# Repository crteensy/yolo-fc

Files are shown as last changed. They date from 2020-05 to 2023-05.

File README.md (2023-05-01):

# Yolo FC, STM32F7, 2-6S
This FC has been test flown with a 3" quad, and it flew well. flight logs of the maiden flight are in /logs

- Main MCU: STM32F745
- IMU: ICM-20602
- Flash: 8MB
- Baro: BMP280
- OSD: '7456
- GNSS: Integrated GPS module (uBlox ZOE-M8Q) with u.Fl connector and experimental support for active antennas
- 4 ESCs:
  - EFM8BB21 / bluejay
  - Calculated current rating of 20A continuous 30A burst (depending on the airflow cooling situation)
- Current sensor: INA186 with 0m5 shunt - subjectively some of the best current measurements we have seen on any FC
- 4 multi purpose expansion connectors:
  - each with its own UART
  - shared I2C bus
  - 5V, 3V3 and GND
  - a multi-purpose pin for analog RSSI, Buzzer, LEDs, etc.
- One video expansion connector:
  - Camera in and VTx out
  - UART
  - 2 multi-purpose pins
  - switchable 5V (*)
- size: 30 x 25.2 mm

The expansion connectors can be used with very simple or more complex plug-ins for
- Rx of your choice
- Magnetometer
- Buzzer
- LED strip
- dual camera switching on the OSD connector
- even additional plugin ESCs for hexa- and octocopters are possible

*) The OSD connector has a 5V output that is only ON when USB is not plugged in. This protects your USB port from power hungry VTx'es that might overload the port. However, that feature can be disabled with a solder bridge.

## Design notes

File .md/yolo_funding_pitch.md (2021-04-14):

# Please Help us Make the Final Yolo FC Prototype Fly

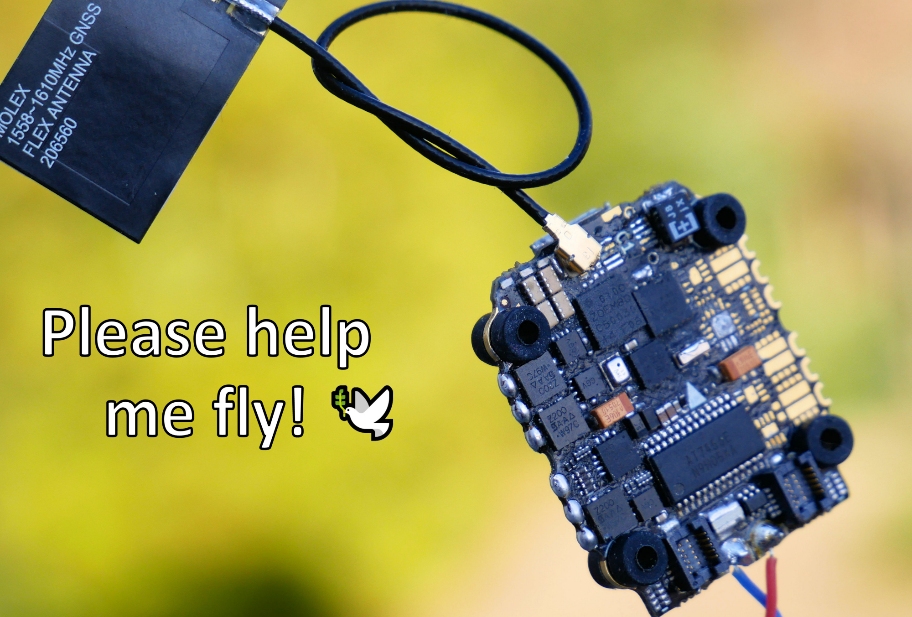
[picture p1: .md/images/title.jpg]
Manually assembled first prototype with GNSS Antenna

First partly by hand assembled prototype of the Yolo. More images at the end of the site.

## The YOLO AIO Flight Controller
The Yolo FC is an 20mm 25A F7 all-in-one flight controller. Initially, it was taylored to fullfill the needs of flight time record-breaking quads, but due to our urge to integrate more and more features made became the most versatile flight controller we can imagine. 
We somehow managed to assemble all functional parts of the first prototype by hand(!) in order to verify their function. For the next step, a second Prototype, we've come to an end of our manual assembly capabilities as well as our financial budget for PCBs and electronic parts. We see electronics design as part of our RC hobby and we don't intend to make any money with this, but our financial capacity is therefore also limited.
Please support us wit a small donation to make the Yolo finally fly!
[GOFUNDME LINK]

## The Specs 
It's actually two AIO FCs for two different battery voltage ranges:
- 1-3S
- 2-6S

What they have in common:
- Main MCU: STM32F745
- IMU: ICM-20602
- Flash: 8MB
- Baro: BMP280
- OSD: '7456 
- GNSS: Integrated GPS-module (uBlox ZOE-M8Q) with u.Fl connector and experimental support for active antennas
- 4 ESCs:
  - BLHeli_S bluejay with a custom firmware
  - Calculated current rating of 20A continuous 30A burst (depending on the airflow cooling situation)
  - up to now, we could only test one ESC with 16 A continuous (> 1 minute), but the whole FC got only slightly warm at this test
- Current sensor: INA186 with 0m5 shunt - subjectively some of the best current measurements we have seen on any FC
- 4 multi purpose expansion connectors:
  - each with its own UART
  - shared I2C bus
  - 5V, 3V3 and GND
  - a multi-purpose pin for analog RSSI, Buzzer, LEDs, etc.
- One video expansion connector:
  - Camera in and VTx out
  - UART
  - 2 multi-purpose pins
  - switchable 5V (*)
- size: 30 x 25.2 mm
- weight: about 4.4 grams + expansions

The expansion connectors can be used with very simple or more complex plug-ins for
- Rx of your choice
- Magnetometer
- Buzzer
- LED strip
- dual camera switching on the OSD connector
- even additional ESC adapters for hexa- and octocopters are possible

*) The OSD connector has a 5V output that is only ON when USB is not plugged in. This protects your USB port from power hungry VTx'es that might overload the port. However, that feature can be disabled with a solder bridge.

The first prototype was assembled manually, on a PCB that we were able to get for free because we had a huge amount of luck. However, it was not perfect, so:
- we want to make a revised layout and have it made
- but we don't want to assemble it manually again for sanity reasons.

Bcause we always have some additional cool RC projects in the pipeline, the prototyping PCB run might also contain:
- enough Yolo PCBs for a prototype batch (if it flies)
- complex YOLO expansions like a 2in1 and a 4in1 ESC for hexas and octos (Why no 45g AUW Hexa Whoop with GPS? Yes the more stupid it sounds, the more fun we have!:-) )
- crteensy's experiments with Cypress PSoC6 for an AIO controller that unifies FC, 4 ESCs and the OSD on one chip (yes, memory mapped ESCs!) in two sizes:
  - whoop for manual assembly, with Bluetooth and USB
  - 16 mm, Bluetooth only
- maybe an H7-Yolo with AM32 ESCs
- maybe an H7 1s tiny whoop board
- (some Express LRS prototypes)

We think that for high quality PCB Panels with custom Layer Stackup and Via in Pad we need about 1500$. A professional prototype assembly of a few flight controllers and the compontens will be about 2500$. If we get more donations than we actually need and The Yolo flies, we will assemble more and send them to testers and  randomly picked donors (we need an e-mail adress in this case).

We don't have any support from the industry, we don't intend to make money with this and all designs will be open hardware for everyone to manufacture.

# Pictures
Current Yolo prototype:

Expansions:

PSoC Whoop board rendering (top/bottom):

PsoC 16 mm board rendering (top/bottom):

ELRS:

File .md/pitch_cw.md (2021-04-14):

## Please help us make the final Yolo FC prototype fly

What started out as a hobby project has brought us to end of our manual assembly capabilities, but we've gotten pretty far with our AIO:

[yolo-pic]

(more pictures at the end of this post)

# The Yolo FC
It's actually two AIO FCs for two different battery voltage ranges:
- 1-3S
- 2-6S

What they have in common:
- Main MCU: STM32F745
- IMU: ICM-20602
- Flash: 8MB
- Baro: BMP280
- OSD: '7456 
- GNSS: uBlox ZOE-M8Q with u.Fl connector and experimental support for active antennas
- 4 ESCs:
  - BLHeli_S bluejay with a custom layout
  - we could only test it to 16 A continuous (> 1 minute) until now, and it didn't burn
- Current sensor: INA186 with 0m5 shunt
- 4 multi purpose expansion connectors:
  - each with its own UART
  - shared I2C bus
  - 5V, 3V3 and GND
  - a multi-purpose pin
- One video expansion connector:
  - Camera in and VTx out
  - UART
  - 2 multi-purpose pins
  - switchable 5V (*)
- size: 30 x 25.2 mm
- weight: about 4.2 grams + expansions

The expansion connectors can be used with very simple or more complex plug-ins for
- Rx of your choice
- Magnetometer
- Buzzer
- LED strip
- in the next layout revision: additional
  - 2in1 ESC for hex copters
  - 4in1 ESC for octo copters
- dual camera switching on the OSD connector

*) The OSD connector has a 5V output that is only ON when USB is not plugged in. This protects your USB port from power hungry VTx'es that might overload the port. However, that feature can be disabled with a solder bridge.

The first prototype was assembled manually, on a PCB that we were able to get for free because we had a huge amount of luck. However, it was not perfect, so:
- we want to make a revised layout and have it made
- but we don't want to assemble it manually again for sanity reasons.

The prototyping run will also contain boards for:
- complex expansions like a 2in1 and a 4in1 ESC
- crteensy's experiments with Cypress PSoC6 for an AIO controller that unifies FC, 4 ESCs and the OSD on one chip (yes, memory mapped ESCs!) in two sizes:
  - whoop for manual assembly, with Bluetooth and USB
  - 16 mm, Bluetooth only
- (some Express LRS prototypes)
- enough Yolo PCBs for a first production run (if it flies)

However, that prototyping panel will be expensive, so we are asking for financial support on [GOFUNDME LINK] to get the PCBs made and a handful of Yolos assembled profesionally; also to send them to testers and random supporters (if we have enough).
If you want to support us, please donate.

We don't have any support from the industry, we don't intend to make money with this and all designs will be open hardware.

# Pictures
Current Yolo prototype:

Expansions:

PSoC Whoop board rendering (top/bottom):

PsoC 16 mm board rendering (top/bottom):

ELRS:

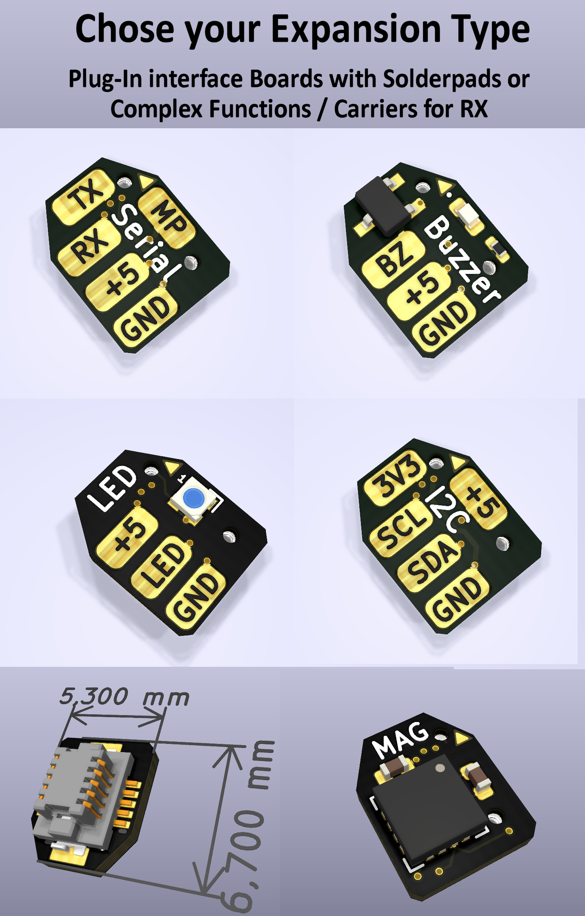
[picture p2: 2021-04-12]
.md/images/expansion_connectors.png

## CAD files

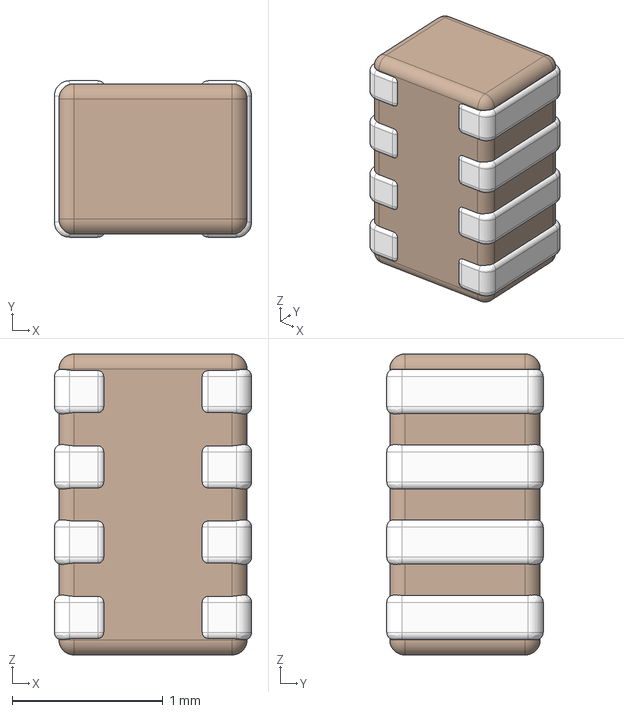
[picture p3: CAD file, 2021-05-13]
kicad/3D/idc.stp
1.31 x 1.04 x 2.00 mm

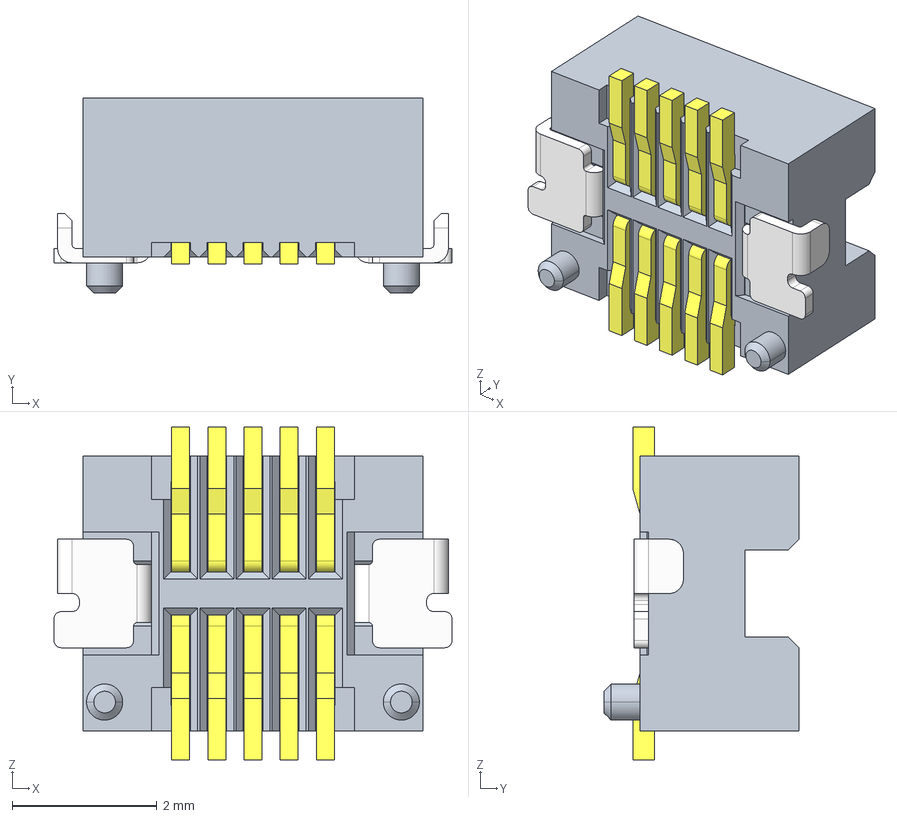
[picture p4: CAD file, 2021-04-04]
kicad/3D/10132797-011100LF.stp
5.50 x 2.70 x 4.60 mm
30H-10PIN-F-H
30H-F-TERMINAL x 5

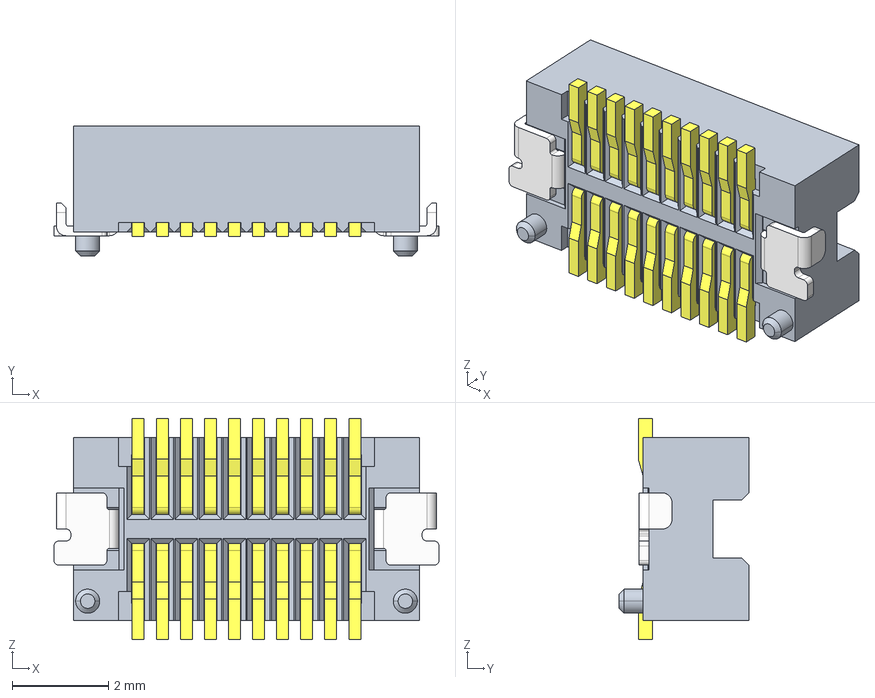
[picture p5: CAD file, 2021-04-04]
kicad/3D/10132797-021100LF.stp
8.00 x 2.70 x 4.60 mm
30H-20PIN-F-H
30H-F-TERMINAL x 10

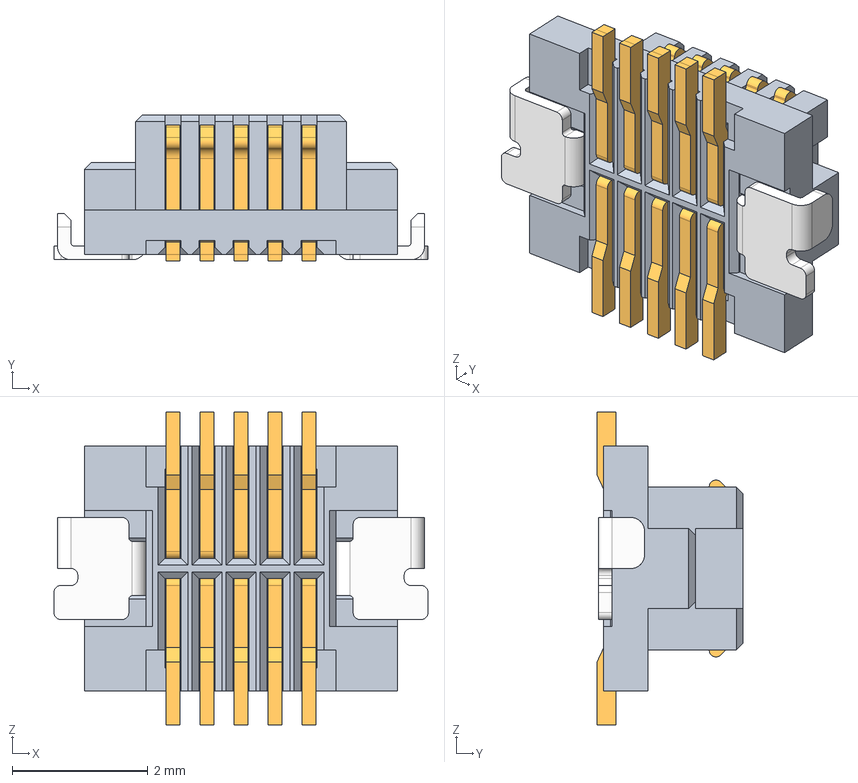
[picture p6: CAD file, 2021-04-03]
kicad/3D/10132798-011110LF.stp
5.50 x 2.15 x 4.60 mm
30H-10PIN-M-H
30H-M-TERMINAL x 5

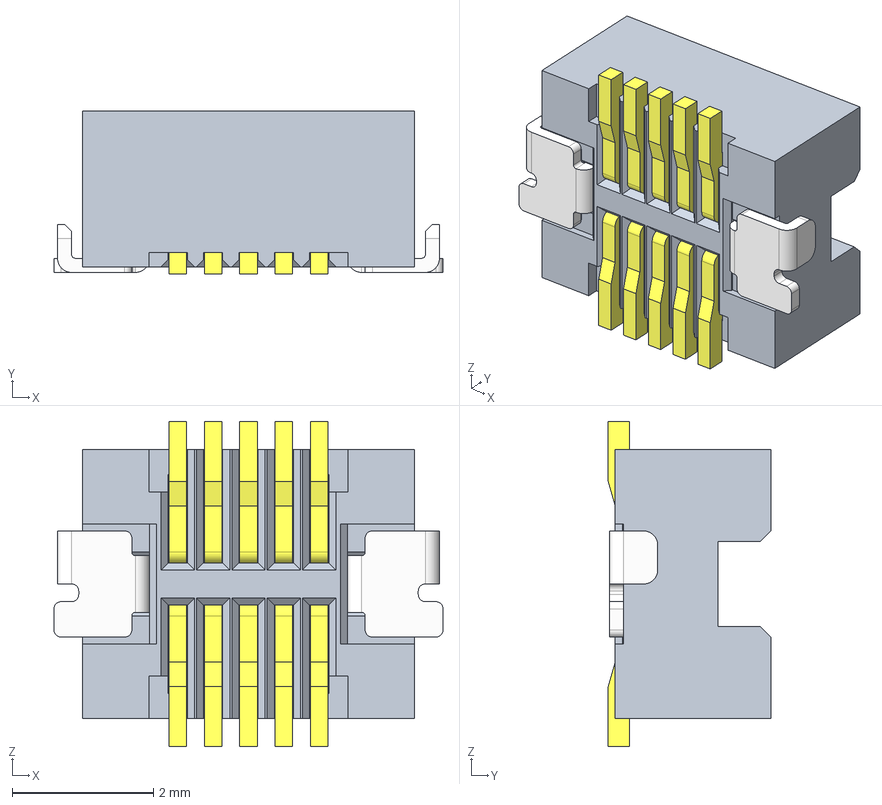
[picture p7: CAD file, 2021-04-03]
kicad/3D/10132797-011110LF.stp
5.50 x 2.30 x 4.60 mm
30H-10PIN-F-H
30H-F-TERMINAL x 5

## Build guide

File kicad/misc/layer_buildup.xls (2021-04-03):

Layer | Type | Thickness
Top | Cu 35µm | 35
 | 2x Prepreg 1080 or similar | 140
In1 | Cu 18µm | 18
 | Core 50 μm | 50
In2 | Cu 18µm | 18
 | 2x Prepreg 1080 or similar | 140
In3 | Cu 35µm | 35
 | Core 50 μm | 50
In4 | Cu 35µm | 35
 | 2x Prepreg 1080 or similar | 140
In5 | Cu 18µm | 18
 | Core 50 μm | 50
IN6 | Cu 18µm | 18
 | 2x Prepreg 1080 or similar | 140
Bot | Cu 35µm | 35
 |  | 922

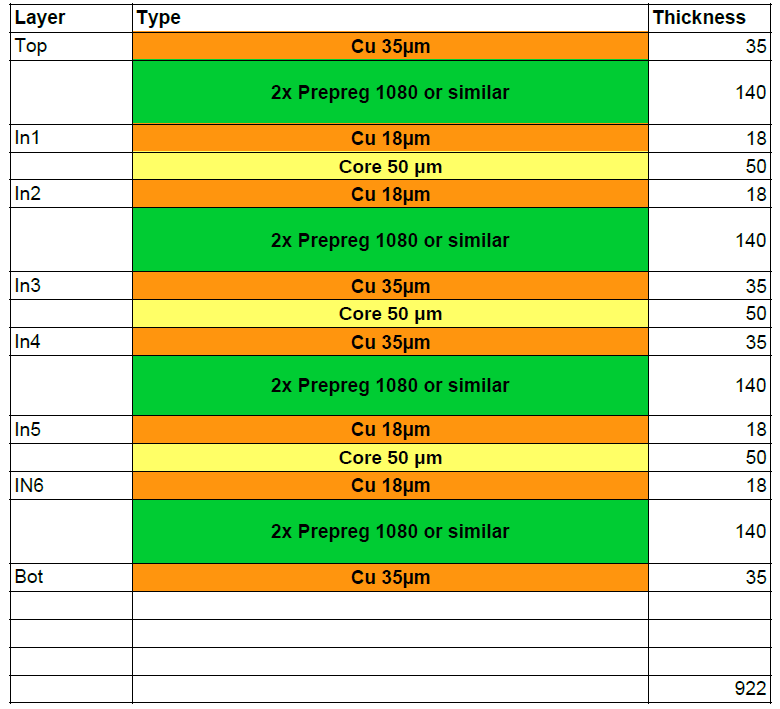
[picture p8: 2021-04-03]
kicad/misc/layer_buildup.png

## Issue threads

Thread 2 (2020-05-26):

Add VUSB voltage divider

crteensy, 2020-05-26:
correct operation needs a V divider from VUSB to sense input

Closed 2023-05-01.

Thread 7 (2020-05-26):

Slightly optional: buzzer output

crteensy, 2020-05-26:
Add buzzer driver FET or provide other means of connecting a buzzer

Closed 2023-05-01.

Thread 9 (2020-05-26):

Clarify ADC full scale input voltage

crteensy, 2020-05-26:
Schematic is drawn for 1.2V full scale, check in BF sources if that's correct.

Closed 2023-05-01.

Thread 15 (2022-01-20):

Fix RN 4x0402 array footprint

crteensy, 2022-01-20:
Fix RN 4x0402 array footprint

Closed 2023-05-01.

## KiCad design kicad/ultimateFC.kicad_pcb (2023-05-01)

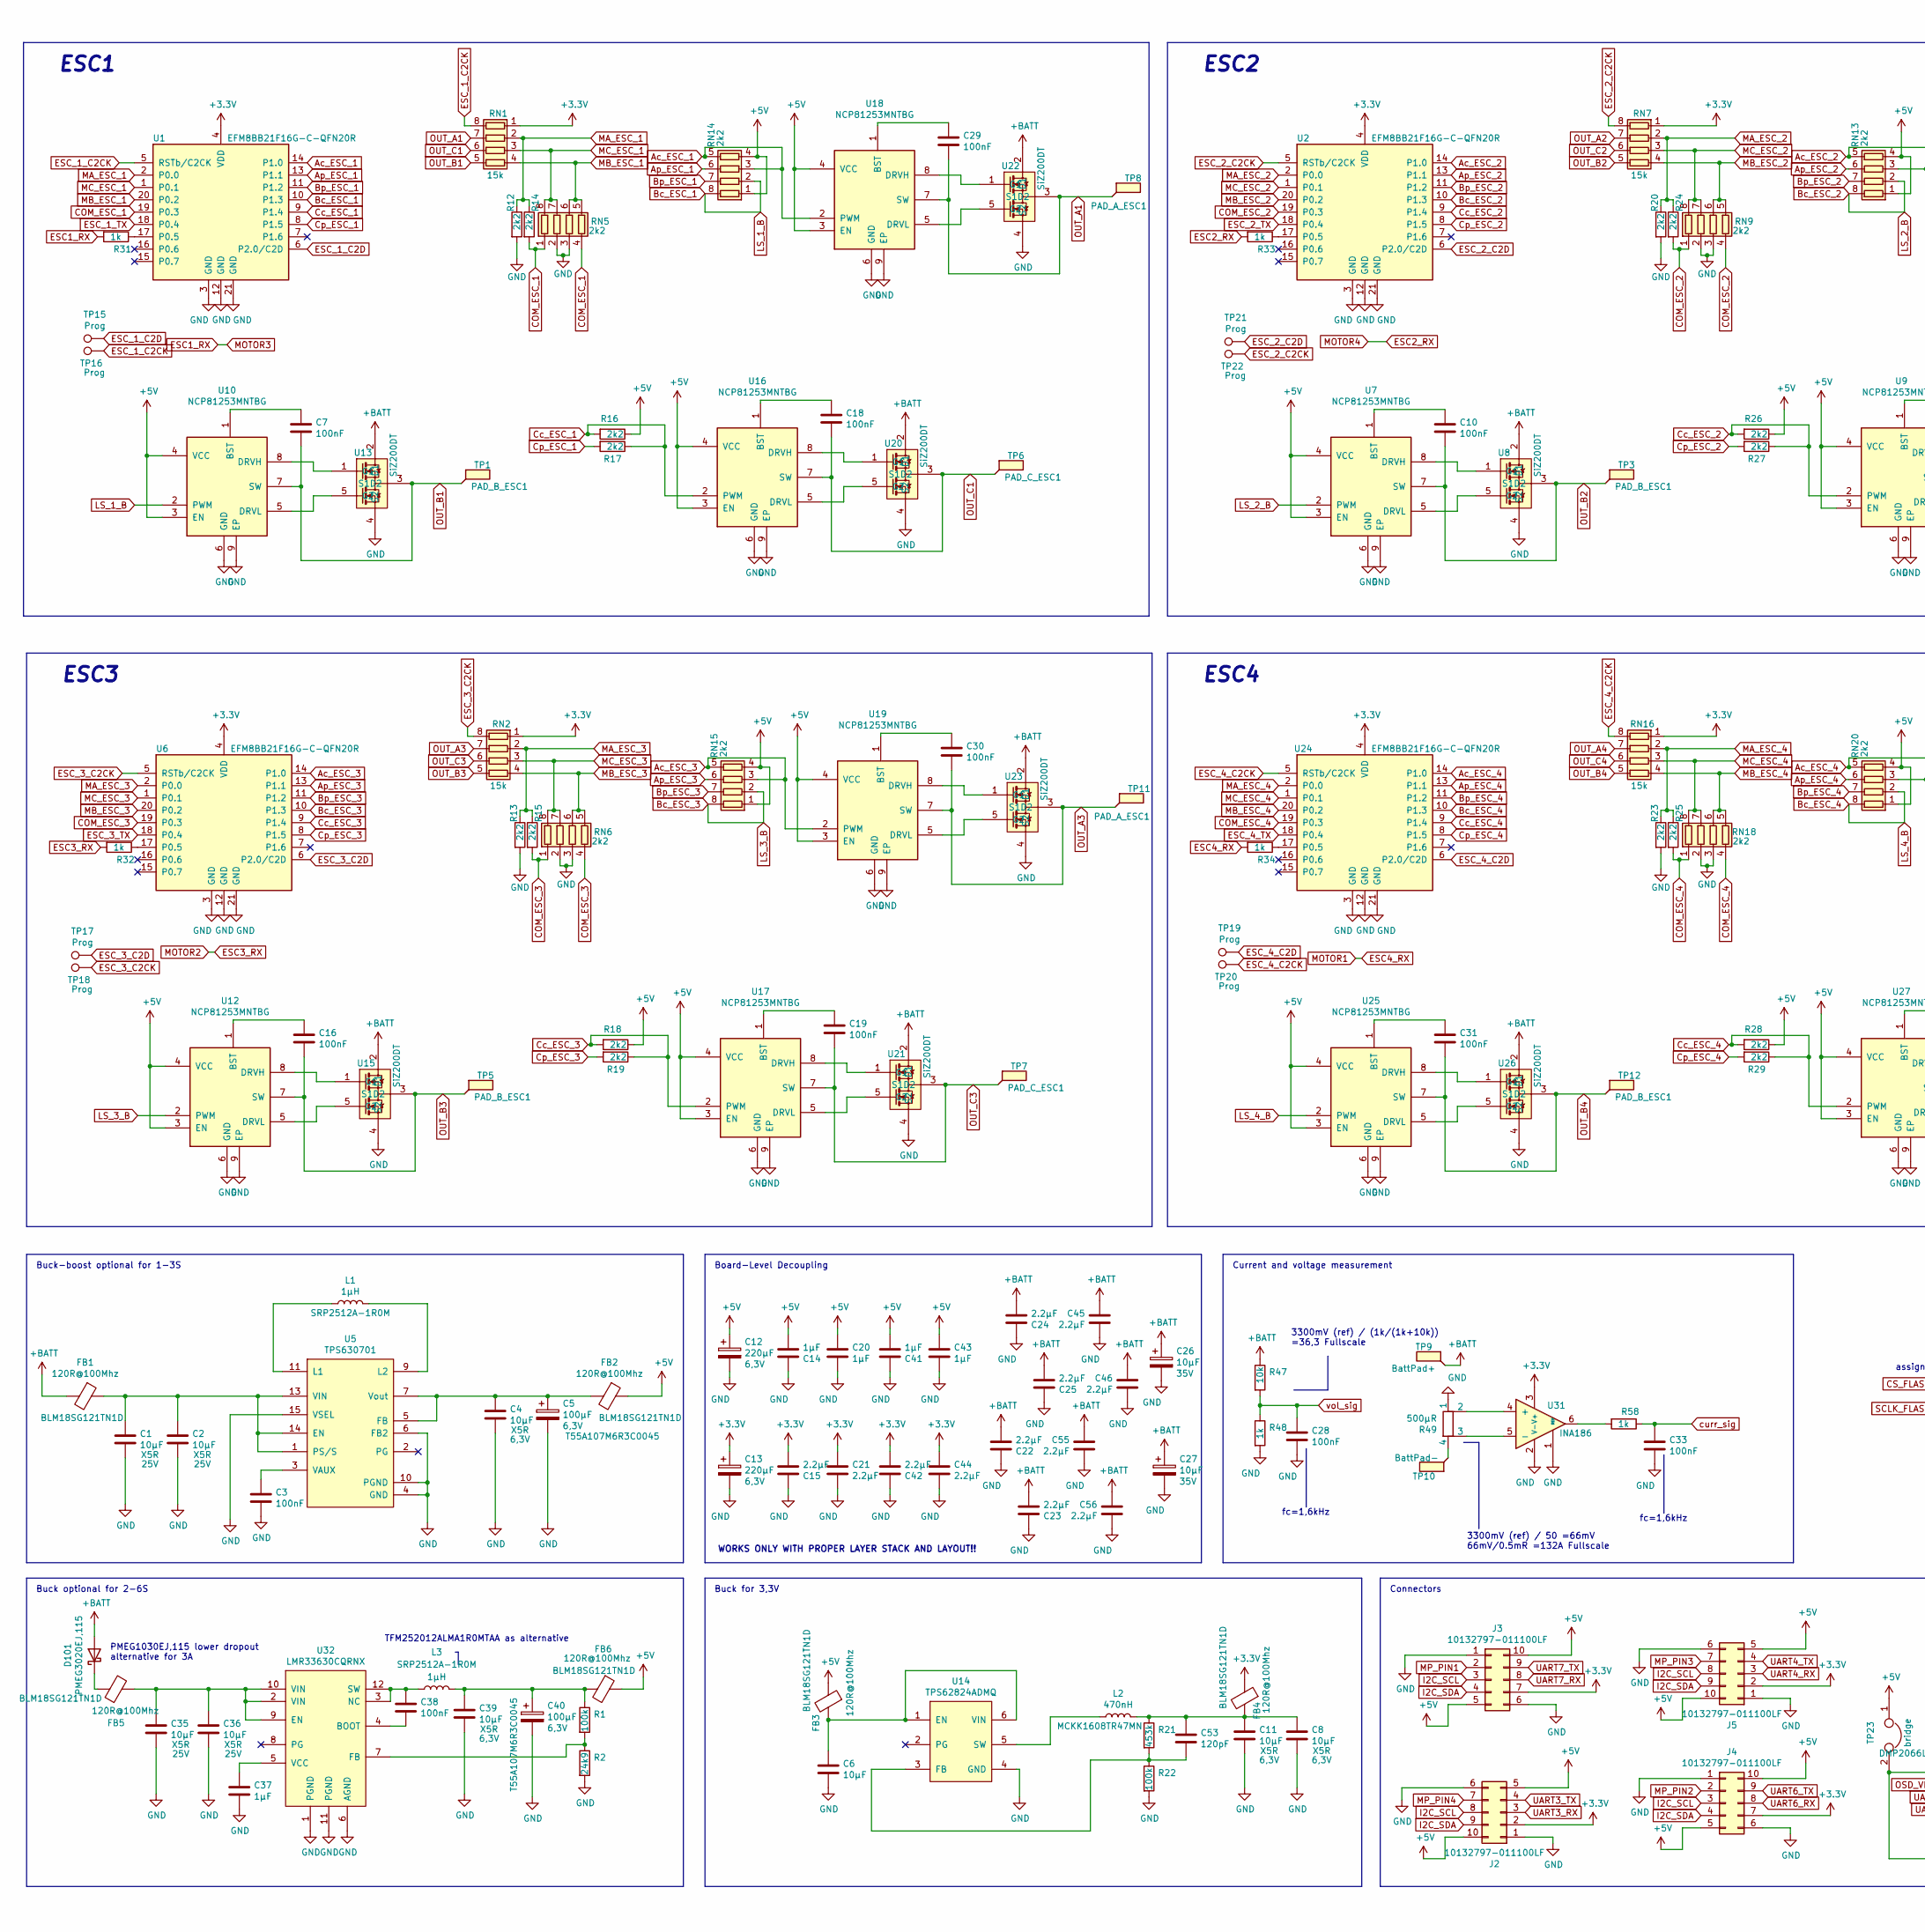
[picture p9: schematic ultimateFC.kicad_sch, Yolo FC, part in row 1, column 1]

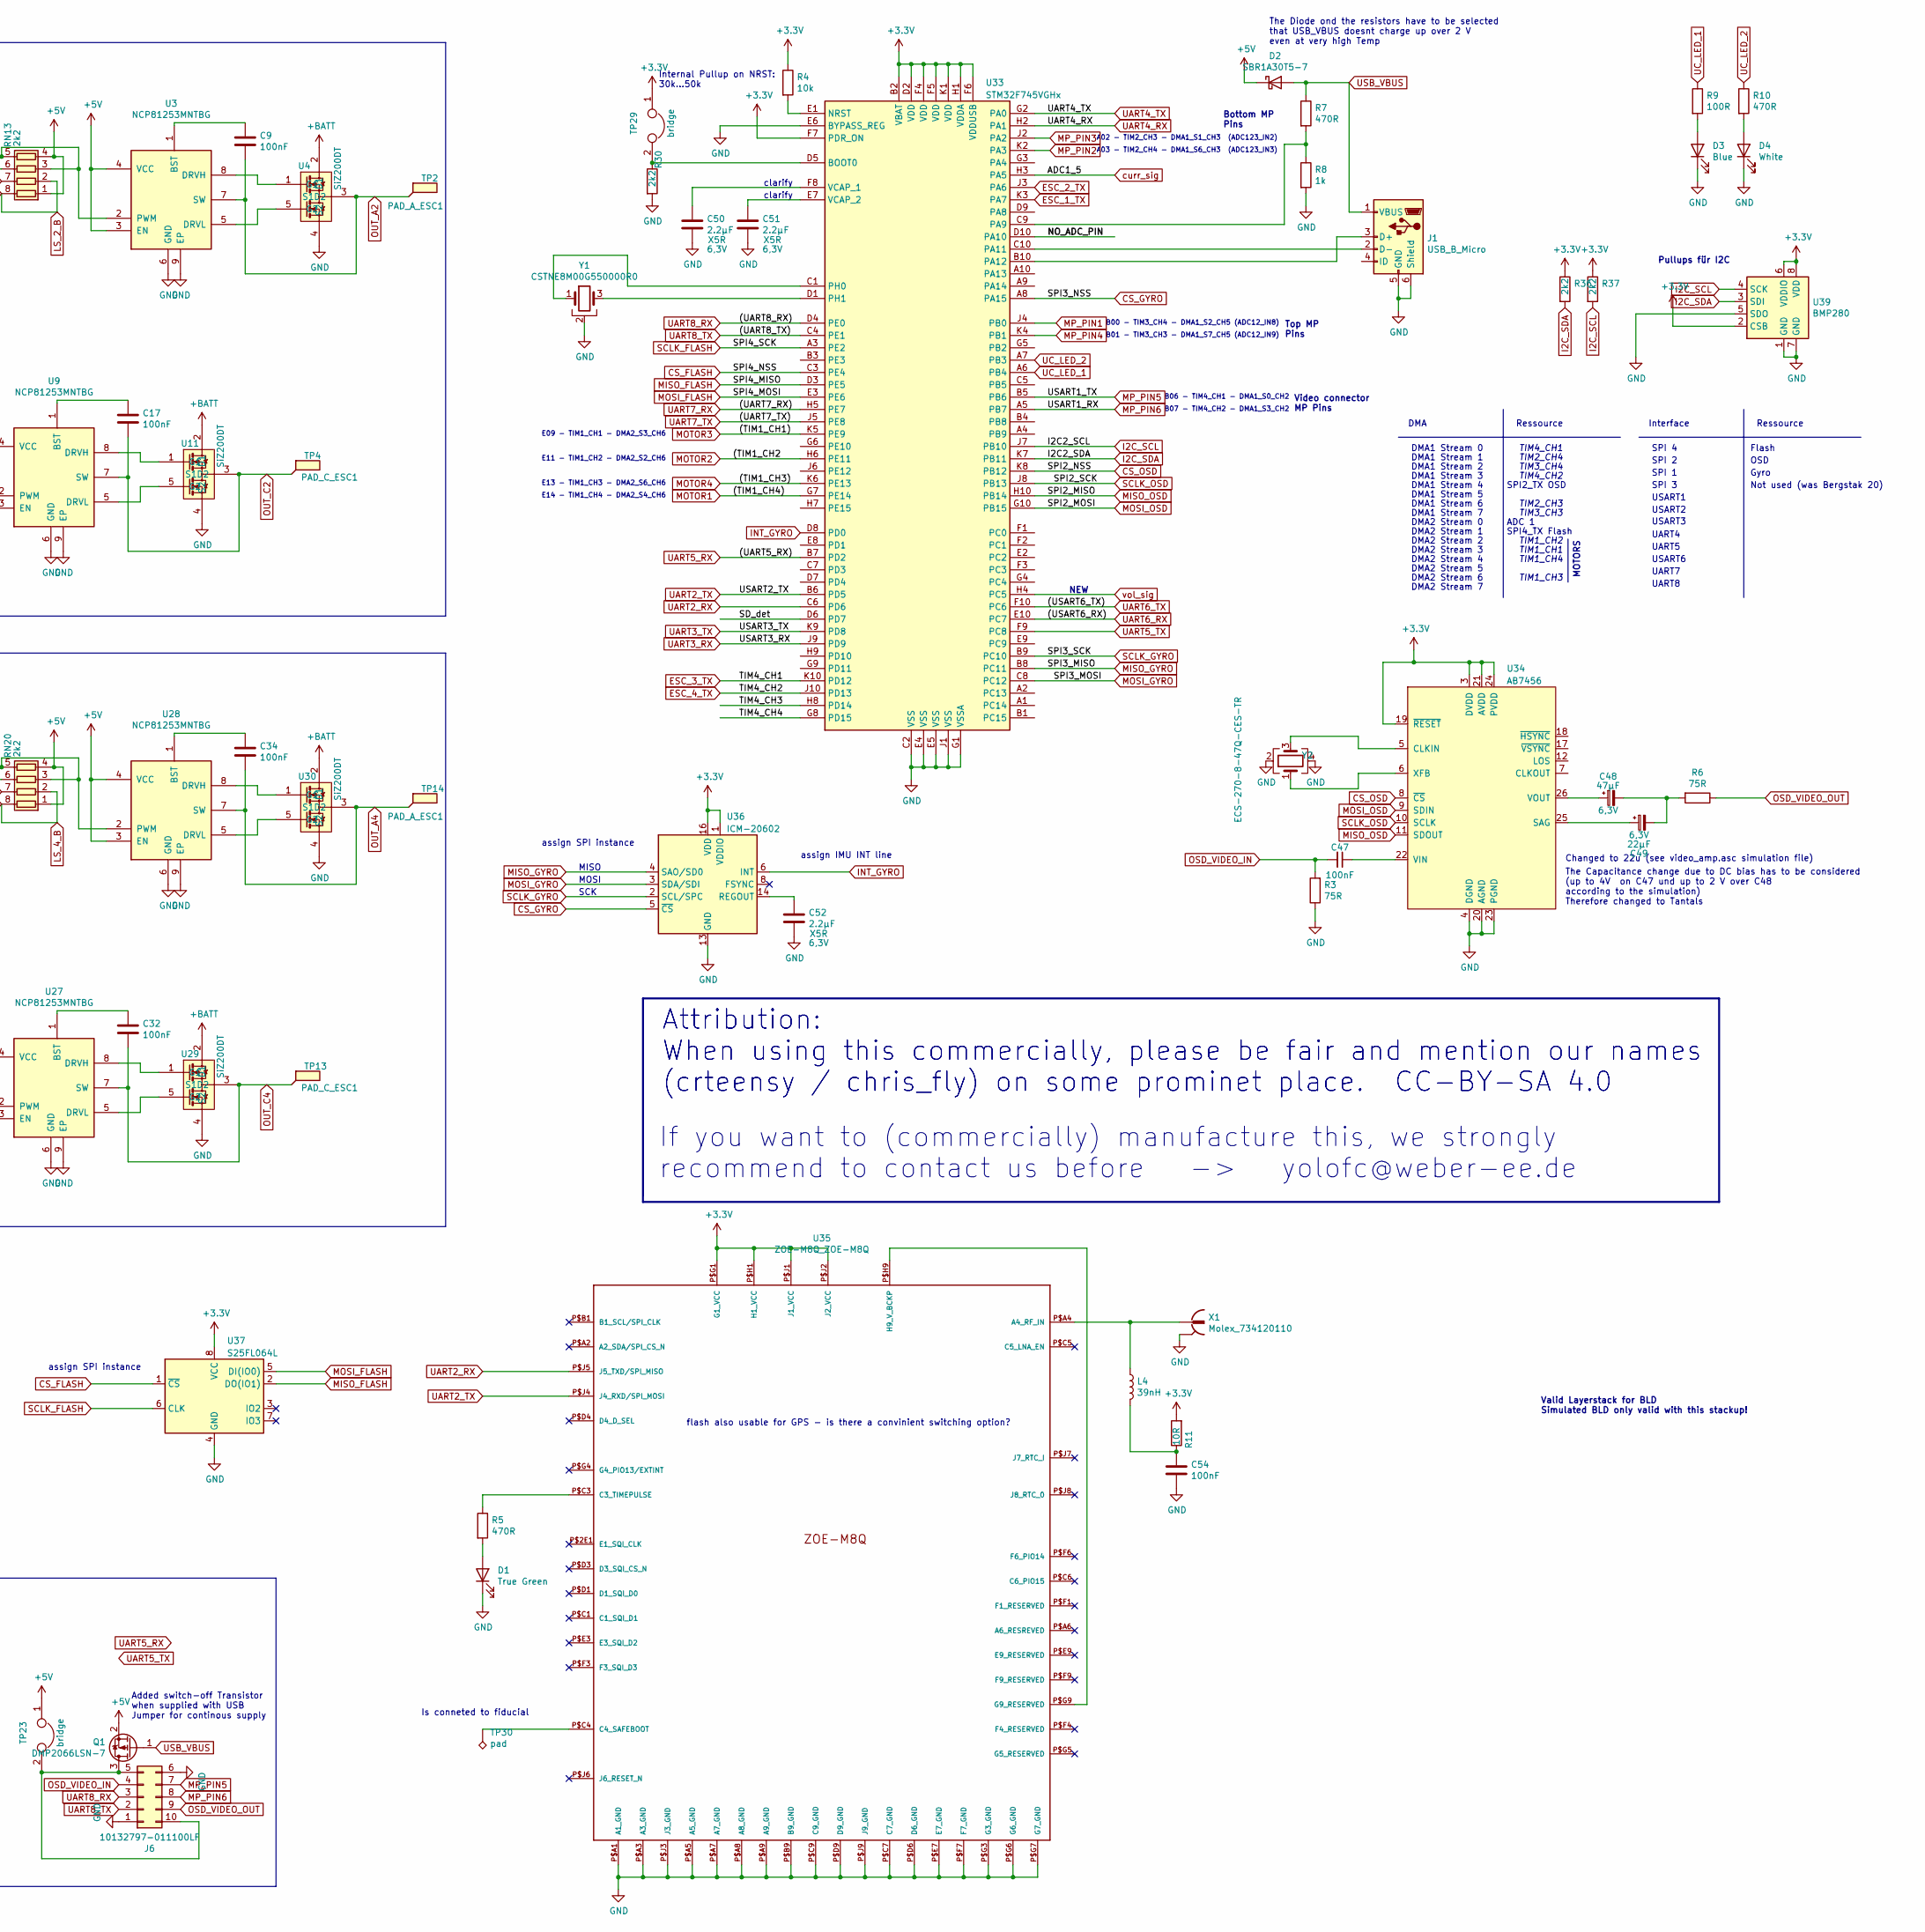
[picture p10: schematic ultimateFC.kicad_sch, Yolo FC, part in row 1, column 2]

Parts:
C1, C2, C35, C36: 10µF; C_1206_3216Metric
C3, C28, C33, C38, C47, C54: 100nF; C_0201_0603Metric_mod
C4, C6, C8, C11, C39: 10µF; C_0603_1608Metric
C5, C40: 100µF; CP_EIA-3216-10_Kemet-I
C7, C9, C10, C16, C17, C18, C19, C29, C30, C31, C32, C34: 100nF; C_0402_1005Metric
C12, C13: 220µF; CP_EIA-3528-15_AVX-H
C14, C20, C41, C43: 1µF; C_AVX_Super_Low_ESL
C15, C21, C42, C44: 2.2µF; C_AVX_Super_Low_ESL
C22, C23, C24, C25, C45, C46, C55, C56: 2.2µF; C_0603_1608Metric
C26, C27: 10µF; CP_EIA-3216-18_Kemet-A
C37: 1µF; C_0402_1005Metric
C48: 47µF; C_0603_1608Metric
C49: 22µF; C_0603_1608Metric
C50, C51, C52: 2.2µF; C_0402_1005Metric
C53: 120pF; C_0201_0603Metric_mod
D1: True Green; LED_0201_0603Metric
D2: SBR1A30T5-7; D_SOD-523
D3: Blue; LED_0201_0603Metric
D4: White; LED_0201_0603Metric
D101: PMEG3020EJ,115; D_SOD-323
FB1, FB2, FB3, FB4, FB5, FB6: 120R@100Mhz; L_0603_1608Metric
J1: USB_B_Micro; USB_Micro-B_Molex_47346-0001
J2, J3, J4, J5, J6: 10132797-011100LF
L1, L3: 1µH; L_Wuerth_MAPI-2506
L2: 470nH; L_0603_1608Metric
L4: 39nH; L_0201_0603Metric
Q1: DMP2066LSN-7; SOT-323_SC-70
R1, R22: 100k; R_0201_0603Metric_mod
R2: 24k9; R_0201_0603Metric_mod
R3, R6: 75R; R_0402_1005Metric
R4: 10k; R_0201_0603Metric_mod
R5, R7, R10: 470R; R_0201_0603Metric_mod
R8, R31, R32, R33, R34, R48, R58: 1k; R_0201_0603Metric_mod
R9: 100R; R_0201_0603Metric_mod
R11: 10R; R_0201_0603Metric_mod
R12, R13, R14, R15, R16, R17, R18, R19, R20, R23, R24, R25, R26, R27, R28, R29, R30, R36, R37: 2k2; R_0201_0603Metric_mod
R21: 453k; R_0201_0603Metric_mod
R47: 10k; R_0402_1005Metric
R49: 500µR; R_Shunt_Vishay_WSKW0612
RN1, RN2, RN7, RN16: 15k; R_Array_Convex_4x0402
RN5, RN6, RN9, RN13, RN14, RN15, RN18, RN20: 2k2; EXB18V_0201x4
TP1, TP3, TP5, TP12: PAD_B_ESC1; esc_pad
TP2, TP8, TP11, TP14: PAD_A_ESC1; esc_pad
TP4, TP6, TP7, TP13: PAD_C_ESC1; esc_pad
TP9: BattPad+; batt_conn_oval
TP10: BattPad-; batt_conn_oval
TP15, TP16, TP17, TP18, TP19, TP20, TP21, TP22: Prog; programm_pad_esc
TP23, TP29: bridge; solderbridge_tiny
TP30: pad; TestPoint_Pad_1.0x1.0mm
U1, U2, U6, U24: EFM8BB21F16G-C-QFN20R; SiliconLabs_QFN-20-1EP_3x3mm_P0.5mm
U3, U7, U9, U10, U12, U16, U17, U18, U19, U25, U27, U28: NCP81253MNTBG; DFN-8-1EP_2x2mm_P0.5mm_EP0.9x1.3mm
U4, U8, U11, U13, U15, U20, U21, U22, U23, U26, U29, U30: SiZ200DT; PowerPAIR3.3x3.3
U5: TPS630701; TEXAS_15-VQFN-HR
U14: TPS62824ADMQ; VSON_HR6
U31: INA186; SOT-363_SC-70-6
U32: LMR33630CQRNX; Texas_RNX0012B
U33: STM32F745VGHx; TFBGA-100_8x8mm_Layout10x10_P0.8mm
U34: AB7456; TSSOP-28_4.4x9.7mm_P0.65mm
U35: ZOE-M8Q_ZOE-M8Q; ZOE-M8
U36: ICM-20602; LGA-16_3x3mm_P0.5mm_LayoutBorder3x5y
U37: S25FL064L; WSON-8_4x4mm_P0.8mm
U39: BMP280; Bosch_LGA-8_2x2.5mm_P0.65mm_ClockwisePinNumbering
X1: Molex_734120110
Y1: CSTNE8M00G550000R0; Resonator_SMD_muRata_CSTxExxV-3Pin_3.0x1.1mm
Y2: ECS-270-8-47Q-CES-TR; ECX-1247Q

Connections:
+3V3: C13.1, C15.2, C21.1, C42.2, C44.1, FB4.1, J2.2, J3.7, J4.7, J5.2, R4.1, R11.2, R36.1, R37.1, RN1.1 (R1.1), RN2.1 (R1.1), RN7.1 (R1.1), RN16.1 (R1.1), TP29.1, U1.4 (VDD), U2.4 (VDD), U6.4 (VDD), U24.4 (VDD), U31.3 (V+), U33.B2 (VBAT), U33.D2 (VDD), U33.F4 (VDD), U33.F5 (VDD), U33.F6 (VDDUSB), U33.F7 (PDR_ON), U33.H1 (VDDA), U33.K1 (VDD), U34.3 (DVDD), U34.19 (~RESET), U34.21 (AVDD), U34.24 (PVDD), U35.P$G1 (G1_VCC), U35.P$H1 (H1_VCC), U35.P$J1 (J1_VCC), U35.P$J2 (J2_VCC), U36.1 (VDDIO), U36.16 (VDD), U37.8 (VCC), U39.2 (CSB), U39.6 (VDDIO), U39.8 (VDD)
+5V: C12.1, C14.2, C20.1, C41.2, C43.1, D2.1 (K), FB2.1, FB3.1, FB6.1, J2.5, J2.10, J3.5, J3.10, J4.5, J4.10, J5.5, J5.10, Q1.2 (S), R16.1, R18.1, R26.1, R28.1, RN13.1 (R1.1), RN13.4 (R4.1), RN14.1 (R1.1), RN14.4 (R4.1), RN15.1 (R1.1), RN15.4 (R4.1), RN20.1 (R1.1), RN20.4 (R4.1), TP23.1, U3.3 (EN), U3.4 (VCC), U7.3 (EN), U7.4 (VCC), U9.3 (EN), U9.4 (VCC), U10.3 (EN), U10.4 (VCC), U12.3 (EN), U12.4 (VCC), U16.3 (EN), U16.4 (VCC), U17.3 (EN), U17.4 (VCC), U18.3 (EN), U18.4 (VCC), U19.3 (EN), U19.4 (VCC), U25.3 (EN), U25.4 (VCC), U27.3 (EN), U27.4 (VCC), U28.3 (EN), U28.4 (VCC)
+BATT: C22.2, C23.2, C24.2, C25.2, C26.1, C27.1, C45.1, C46.1, C55.1, C56.1, D101.2 (A), FB1.2, R47.1, TP9.1, U4.2 (D1), U8.2 (D1), U11.2 (D1), U13.2 (D1), U15.2 (D1), U20.2 (D1), U21.2 (D1), U22.2 (D1), U23.2 (D1), U26.2 (D1), U29.2 (D1), U30.2 (D1)
/NO_ADC_PIN: U33.D10 (PA10)
/SD_det: U33.D6 (PD7)
/TIM4_CH3: U33.H8 (PD14)
/TIM4_CH4: U33.G8 (PD15)
Ac_ESC_1: RN14.3 (R3.1), RN14.5 (R4.2), U1.14 (P1.0), U18.2 (PWM)
Ac_ESC_2: RN13.3 (R3.1), RN13.5 (R4.2), U2.14 (P1.0), U3.2 (PWM)
Ac_ESC_3: RN15.3 (R3.1), RN15.5 (R4.2), U6.14 (P1.0), U19.2 (PWM)
Ac_ESC_4: RN20.3 (R3.1), RN20.5 (R4.2), U24.14 (P1.0), U28.2 (PWM)
Ap_ESC_1: RN14.6 (R3.2), U1.13 (P1.1)
Ap_ESC_2: RN13.6 (R3.2), U2.13 (P1.1)
Ap_ESC_3: RN15.6 (R3.2), U6.13 (P1.1)
Ap_ESC_4: RN20.6 (R3.2), U24.13 (P1.1)
Bc_ESC_1: RN14.2 (R2.1), RN14.8 (R1.2), U1.10 (P1.3), U10.2 (PWM)
Bc_ESC_2: RN13.2 (R2.1), RN13.8 (R1.2), U2.10 (P1.3), U7.2 (PWM)
Bc_ESC_3: RN15.2 (R2.1), RN15.8 (R1.2), U6.10 (P1.3), U12.2 (PWM)
Bc_ESC_4: RN20.2 (R2.1), RN20.8 (R1.2), U24.10 (P1.3), U25.2 (PWM)
Bp_ESC_1: RN14.7 (R2.2), U1.11 (P1.2)
Bp_ESC_2: RN13.7 (R2.2), U2.11 (P1.2)
Bp_ESC_3: RN15.7 (R2.2), U6.11 (P1.2)
Bp_ESC_4: RN20.7 (R2.2), U24.11 (P1.2)
COM_ESC_1: R14.2, RN5.1 (R1.1), RN5.4 (R4.1), U1.19 (P0.3)
COM_ESC_2: R24.2, RN9.1 (R1.1), RN9.4 (R4.1), U2.19 (P0.3)
COM_ESC_3: R15.2, RN6.1 (R1.1), RN6.4 (R4.1), U6.19 (P0.3)
COM_ESC_4: R25.2, RN18.1 (R1.1), RN18.4 (R4.1), U24.19 (P0.3)
CS_FLASH: U33.C3 (PE4), U37.1 (~CS)
CS_GYRO: U33.A8 (PA15), U36.5 (~CS)
CS_OSD: U33.K8 (PB12), U34.8 (~CS)
Cc_ESC_1: R16.2, R17.1, U1.9 (P1.4), U16.2 (PWM)
Cc_ESC_2: R26.2, R27.1, U2.9 (P1.4), U9.2 (PWM)
Cc_ESC_3: R18.2, R19.1, U6.9 (P1.4), U17.2 (PWM)
Cc_ESC_4: R28.2, R29.1, U24.9 (P1.4), U27.2 (PWM)
Cp_ESC_1: R17.2, U1.8 (P1.5)
Cp_ESC_2: R27.2, U2.8 (P1.5)
Cp_ESC_3: R19.2, U6.8 (P1.5)
Cp_ESC_4: R29.2, U24.8 (P1.5)
ESC1_RX: R31.2, U33.K5 (PE9)
ESC2_RX: R33.2, U33.K6 (PE13)
ESC3_RX: R32.2, U33.H6 (PE11)
ESC4_RX: R34.2, U33.G7 (PE14)
ESC_1_C2CK: RN1.8 (R1.2), TP16.1, U1.5 (RSTb/C2CK)
ESC_1_C2D: TP15.1, U1.6 (P2.0/C2D)
ESC_1_TX: U1.18 (P0.4), U33.K3 (PA7)
ESC_2_C2CK: RN7.8 (R1.2), TP22.1, U2.5 (RSTb/C2CK)
ESC_2_C2D: TP21.1, U2.6 (P2.0/C2D)
ESC_2_TX: U2.18 (P0.4), U33.J3 (PA6)
ESC_3_C2CK: RN2.8 (R1.2), TP18.1, U6.5 (RSTb/C2CK)
ESC_3_C2D: TP17.1, U6.6 (P2.0/C2D)
ESC_3_TX: U6.18 (P0.4), U33.K10 (PD12)
ESC_4_C2CK: RN16.8 (R1.2), TP20.1, U24.5 (RSTb/C2CK)
ESC_4_C2D: TP19.1, U24.6 (P2.0/C2D)
ESC_4_TX: U24.18 (P0.4), U33.J10 (PD13)
GND: C1.2, C2.2, C3.2, C4.2, C5.2, C6.2, C8.2, C11.2, C12.2, C13.2, C14.1, C15.1, C20.2, C21.2, C22.1, C23.1, C24.1, C25.1, C26.2, C27.2, C28.2, C33.2, C35.2, C36.2, C37.2, C39.2, C40.2, C41.1, C42.1, C43.2, C44.2, C45.2, C46.2, C50.2, C51.2, C52.2, C54.2, C55.2, C56.2, D1.1 (K), D3.1 (K), D4.1 (K), J1.5 (GND), J1.6 (Shield), J2.1, J2.6, J3.1, J3.6, J4.1, J4.6, J5.1, J5.6, J6.1, J6.6, R2.2, R3.1, R8.2, R12.2, R13.2, R20.2, R22.2, R23.2, R30.2, R48.2, R49.1, RN5.2 (R2.1), RN5.3 (R3.1), RN6.2 (R2.1), RN6.3 (R3.1), RN9.2 (R2.1), RN9.3 (R3.1), RN18.2 (R2.1), RN18.3 (R3.1), U1.3 (GND), U1.12 (GND), U1.21 (GND), U2.3 (GND), U2.12 (GND), U2.21 (GND), U3.6 (GND), U3.9 (EP), U4.4 (S2), U5.4 (GND), U5.6 (FB2), U5.10 (PGND), U5.15 (VSEL), U6.3 (GND), U6.12 (GND), U6.21 (GND), U7.6 (GND), U7.9 (EP), U8.4 (S2), U9.6 (GND), U9.9 (EP), U10.6 (GND), U10.9 (EP), U11.4 (S2), U12.6 (GND), U12.9 (EP), U13.4 (S2), U14.4 (GND), U15.4 (S2), U16.6 (GND), U16.9 (EP), U17.6 (GND), U17.9 (EP), U18.6 (GND), U18.9 (EP), U19.6 (GND), U19.9 (EP), U20.4 (S2), U21.4 (S2), U22.4 (S2), U23.4 (S2), U24.3 (GND), U24.12 (GND), U24.21 (GND), U25.6 (GND), U25.9 (EP), U26.4 (S2), U27.6 (GND), U27.9 (EP), U28.6 (GND), U28.9 (EP), U29.4 (S2), U30.4 (S2), U31.1 (REF), U31.2 (V-), U32.1 (PGND), U32.6 (AGND), U32.11 (PGND), U33.C2 (VSS), U33.E4 (VSS), U33.E5 (VSS), U33.E6 (BYPASS_REG), U33.G1 (VSSA), U33.J1 (VSS), U34.4 (DGND), U34.20 (AGND), U34.23 (PGND), U35.P$A1 (A1_GND), U35.P$A3 (A3_GND), U35.P$A5 (A5_GND), U35.P$A7 (A7_GND), U35.P$A8 (A8_GND), U35.P$A9 (A9_GND), U35.P$B9 (B9_GND), U35.P$C7 (C7_GND), U35.P$C9 (C9_GND), U35.P$D6 (D6_GND), U35.P$D9 (D9_GND), U35.P$E7 (E7_GND), U35.P$F7 (F7_GND), U35.P$G3 (G3_GND), U35.P$G6 (G6_GND), U35.P$G7 (G7_GND), U35.P$J3 (J3_GND), U35.P$J9 (J9_GND), U36.9 (GND), U36.10 (GND), U36.11 (GND), U36.12 (GND), U36.13 (GND), U36.15 (GND), U37.4 (GND), U39.1 (GND), U39.5 (SDO), U39.7 (GND), X1.S@1 (2), X1.S@2 (2), X1.S@3 (2), Y1.2, Y2.2, Y2.4
I2C_SCL: J2.8, J3.3, J4.3, J5.8, R37.2, U33.J7 (PB10), U39.4 (SCK)
I2C_SDA: J2.9, J3.4, J4.4, J5.9, R36.2, U33.K7 (PB11), U39.3 (SDI)
INT_GYRO: U33.D8 (PD0), U36.6 (INT)
MA_ESC_1: R12.1, R14.1, RN1.2 (R2.1), U1.2 (P0.0)
MA_ESC_2: R20.1, R24.1, RN7.2 (R2.1), U2.2 (P0.0)
MA_ESC_3: R13.1, R15.1, RN2.2 (R2.1), U6.2 (P0.0)
MA_ESC_4: R23.1, R25.1, RN16.2 (R2.1), U24.2 (P0.0)
MB_ESC_1: RN1.4 (R4.1), RN5.5 (R4.2), RN5.6 (R3.2), U1.20 (P0.2)
MB_ESC_2: RN7.4 (R4.1), RN9.5 (R4.2), RN9.6 (R3.2), U2.20 (P0.2)
MB_ESC_3: RN2.4 (R4.1), RN6.5 (R4.2), RN6.6 (R3.2), U6.20 (P0.2)
MB_ESC_4: RN16.4 (R4.1), RN18.5 (R4.2), RN18.6 (R3.2), U24.20 (P0.2)
MC_ESC_1: RN1.3 (R3.1), RN5.7 (R2.2), RN5.8 (R1.2), U1.1 (P0.1)
MC_ESC_2: RN7.3 (R3.1), RN9.7 (R2.2), RN9.8 (R1.2), U2.1 (P0.1)
MC_ESC_3: RN2.3 (R3.1), RN6.7 (R2.2), RN6.8 (R1.2), U6.1 (P0.1)
MC_ESC_4: RN16.3 (R3.1), RN18.7 (R2.2), RN18.8 (R1.2), U24.1 (P0.1)
MISO_FLASH: U33.D3 (PE5), U37.2 (DO(IO1))
MISO_GYRO: U33.B8 (PC11), U36.4 (SAO/SD0)
MISO_OSD: U33.H10 (PB14), U34.11 (SDOUT)
MOSI_FLASH: U33.E3 (PE6), U37.5 (DI(IO0))
MOSI_GYRO: U33.C8 (PC12), U36.3 (SDA/SDI)
MOSI_OSD: U33.G10 (PB15), U34.9 (SDIN)
MP_PIN1: J3.2, U33.J4 (PB0)
MP_PIN2: J4.2, U33.K2 (PA3)
MP_PIN3: J5.7, U33.J2 (PA2)
MP_PIN4: J2.7, U33.K4 (PB1)
MP_PIN5: J6.7, U33.B5 (PB6)
MP_PIN6: J6.8, U33.A5 (PB7)
unnamed: C1.1, C2.1, FB1.1, U5.1 (PS/S), U5.13 (VIN), U5.14 (EN)
unnamed: C3.1, U5.3 (VAUX)
unnamed: C4.1, C5.1, FB2.2, U5.5 (FB), U5.7 (Vout)
unnamed: C6.1, FB3.2, U14.1 (EN), U14.6 (VIN)
unnamed: C7.1, U10.1 (BST)
unnamed: C9.1, U3.1 (BST)
unnamed: C10.1, U7.1 (BST)
unnamed: C8.1, C11.1, C53.1, FB4.2, L2.2, R21.1
unnamed: C16.1, U12.1 (BST)
unnamed: C17.1, U9.1 (BST)
unnamed: C18.1, U16.1 (BST)
unnamed: C19.1, U17.1 (BST)
unnamed: C29.1, U18.1 (BST)
unnamed: C30.1, U19.1 (BST)
unnamed: C31.1, U25.1 (BST)
unnamed: C32.1, U27.1 (BST)
unnamed: C34.1, U28.1 (BST)
unnamed: C35.1, C36.1, FB5.2, U32.2 (VIN), U32.9 (EN), U32.10 (VIN)
unnamed: C37.1, U32.5 (VCC)
unnamed: C38.1, L3.1, U32.3 (NC), U32.12 (SW)
unnamed: C38.2, U32.4 (BOOT)
unnamed: C39.1, C40.1, FB6.2, L3.2, R1.1
unnamed: C47.1, U34.22 (VIN)
unnamed: C48.1, U34.26 (VOUT)
unnamed: C48.2, C49.2, R6.2
unnamed: C49.1, U34.25 (SAG)
unnamed: C50.1, U33.F8 (VCAP_1)
unnamed: C51.1, U33.E7 (VCAP_2)
unnamed: C52.1, U36.14 (REGOUT)
unnamed: C53.2, R21.2, R22.1, U14.3 (FB)
unnamed: C54.1, L4.2, R11.1
unnamed: D1.2 (A), R5.2
unnamed: D3.2 (A), R9.2
unnamed: D4.2 (A), R10.2
unnamed: D101.1 (K), FB5.1
unnamed: J1.2 (D-), U33.C10 (PA11)
unnamed: J1.3 (D+), U33.B10 (PA12)
unnamed: J6.5, J6.10, Q1.3 (D), TP23.2
unnamed: L1.1, U5.11 (L1)
unnamed: L1.2, U5.9 (L2)
unnamed: L2.1, U14.5 (SW)
unnamed: L4.1, U35.P$A4 (A4_RF_IN), X1.1
unnamed: R1.2, R2.1, U32.7 (FB)
unnamed: R4.2, U33.E1 (NRST)
unnamed: R5.1, U35.P$C3 (C3_TIMEPULSE)
unnamed: R7.2, R8.1, U33.C9 (PA9)
unnamed: R30.1, TP29.2, U33.D5 (BOOT0)
unnamed: R31.1, U1.17 (P0.5)
unnamed: R32.1, U6.17 (P0.5)
unnamed: R33.1, U2.17 (P0.5)
unnamed: R34.1, U24.17 (P0.5)
unnamed: R49.2, U31.4 (+)
unnamed: R49.3, U31.5 (-)
unnamed: R49.4, TP10.1
unnamed: R58.2, U31.6
unnamed: TP30.1, U35.P$C4 (C4_SAFEBOOT)
unnamed: U3.5 (DRVL), U4.5 (G2)
unnamed: U3.8 (DRVH), U4.1 (G1)
unnamed: U7.5 (DRVL), U8.5 (G2)
unnamed: U7.8 (DRVH), U8.1 (G1)
unnamed: U10.5 (DRVL), U13.5 (G2)
unnamed: U10.8 (DRVH), U13.1 (G1)
unnamed: U9.8 (DRVH), U11.1 (G1)
unnamed: U9.5 (DRVL), U11.5 (G2)
unnamed: U12.5 (DRVL), U15.5 (G2)
unnamed: U12.8 (DRVH), U15.1 (G1)
unnamed: U16.5 (DRVL), U20.5 (G2)
unnamed: U16.8 (DRVH), U20.1 (G1)
unnamed: U17.5 (DRVL), U21.5 (G2)
unnamed: U17.8 (DRVH), U21.1 (G1)
unnamed: U18.5 (DRVL), U22.5 (G2)
unnamed: U18.8 (DRVH), U22.1 (G1)
unnamed: U19.5 (DRVL), U23.5 (G2)
unnamed: U19.8 (DRVH), U23.1 (G1)
unnamed: U25.5 (DRVL), U26.5 (G2)
unnamed: U25.8 (DRVH), U26.1 (G1)
unnamed: U27.5 (DRVL), U29.5 (G2)
unnamed: U27.8 (DRVH), U29.1 (G1)
unnamed: U28.5 (DRVL), U30.5 (G2)
unnamed: U28.8 (DRVH), U30.1 (G1)
unnamed: U33.C1 (PH0), Y1.1
unnamed: U33.D1 (PH1), Y1.3
unnamed: U34.5 (CLKIN), Y2.3
unnamed: U34.6 (XFB), Y2.1
unnamed: U35.P$G9 (G9_RESERVED), U35.P$H9 (H9_V_BCKP)
OSD_VIDEO_IN: C47.2, J6.4, R3.2
OSD_VIDEO_OUT: J6.9, R6.1
OUT_A1: C29.2, RN1.7 (R2.2), TP8.1, U18.7 (SW), U22.3 (S1D2)
OUT_A2: C9.2, RN7.7 (R2.2), TP2.1, U3.7 (SW), U4.3 (S1D2)
OUT_A3: C30.2, RN2.7 (R2.2), TP11.1, U19.7 (SW), U23.3 (S1D2)
OUT_A4: C34.2, RN16.7 (R2.2), TP14.1, U28.7 (SW), U30.3 (S1D2)
OUT_B1: C7.2, RN1.5 (R4.2), TP1.1, U10.7 (SW), U13.3 (S1D2)
OUT_B2: C10.2, RN7.5 (R4.2), TP3.1, U7.7 (SW), U8.3 (S1D2)
OUT_B3: C16.2, RN2.5 (R4.2), TP5.1, U12.7 (SW), U15.3 (S1D2)
OUT_B4: C31.2, RN16.5 (R4.2), TP12.1, U25.7 (SW), U26.3 (S1D2)
OUT_C1: C18.2, RN1.6 (R3.2), TP6.1, U16.7 (SW), U20.3 (S1D2)
OUT_C2: C17.2, RN7.6 (R3.2), TP4.1, U9.7 (SW), U11.3 (S1D2)
OUT_C3: C19.2, RN2.6 (R3.2), TP7.1, U17.7 (SW), U21.3 (S1D2)
OUT_C4: C32.2, RN16.6 (R3.2), TP13.1, U27.7 (SW), U29.3 (S1D2)
SCLK_FLASH: U33.A3 (PE2), U37.6 (CLK)
SCLK_GYRO: U33.B9 (PC10), U36.2 (SCL/SPC)
SCLK_OSD: U33.J8 (PB13), U34.10 (SCLK)
UART2_RX: U33.C6 (PD6), U35.P$J5 (J5_TXD/SPI_MISO)
UART2_TX: U33.B6 (PD5), U35.P$J4 (J4_RXD/SPI_MOSI)
UART3_RX: J2.3, U33.J9 (PD9)
UART3_TX: J2.4, U33.K9 (PD8)
UART4_RX: J5.3, U33.H2 (PA1)
UART4_TX: J5.4, U33.G2 (PA0)
UART5_RX: U33.B7 (PD2)
UART5_TX: U33.F9 (PC8)
UART6_RX: J4.8, U33.E10 (PC7)
UART6_TX: J4.9, U33.F10 (PC6)
UART7_RX: J3.8, U33.H5 (PE7)
UART7_TX: J3.9, U33.J5 (PE8)
UART8_RX: J6.3, U33.D4 (PE0)
UART8_TX: J6.2, U33.C4 (PE1)
UC_LED_1: R9.1, U33.A6 (PB4)
UC_LED_2: R10.1, U33.A7 (PB3)
USB_VBUS: D2.2 (A), J1.1 (VBUS), Q1.1 (G), R7.1
curr_sig: C33.1, R58.1, U33.H3 (PA5)
vol_sig: C28.1, R47.2, R48.1, U33.H4 (PC5)

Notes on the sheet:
Added switch-off Transistor when supplied with USB Jumper for continous supply
E14 - TIM1_CH4 - DMA2_S4_CH6
The Capacitance change due to DC bias has to be considered (up to 4V on C47 und up to 2 V over C48 according to the simulation) Therefore changed to Tantals
3300mV (ref) / 50 =66mV 66mV/0.5mR =132A Fullscale
Internal Pullup on NRST: 30k...50k
MOTORS
clarify
DMA1 Stream 3
DMA1 Stream 4
Video connector MP Pins
ESC3
UART8
DMA1 Stream 6
SPI 1
TIM4_CH1
E09 - TIM1_CH1 - DMA2_S3_CH6
SCK
TIM1_CH4
DMA2 Stream 2
TIM2_CH4
WORKS ONLY WITH PROPER LAYER STACK AND LAYOUT!!
Bottom MP Pins
ESC2
MOSI
Ressource
assign SPI instance
DMA2 Stream 1
ADC 1
fc=1,6kHz
Gyro
UART4
USART3
B06 - TIM4_CH1 - DMA1_S0_CH2
E11 - TIM1_CH2 - DMA2_S2_CH6
E13 - TIM1_CH3 - DMA2_S6_CH6
DMA2 Stream 6
ESC1
PMEG1030EJ,115 lower dropout alternative for 3A
TIM1_CH1
Buck-boost optional for 1-3S

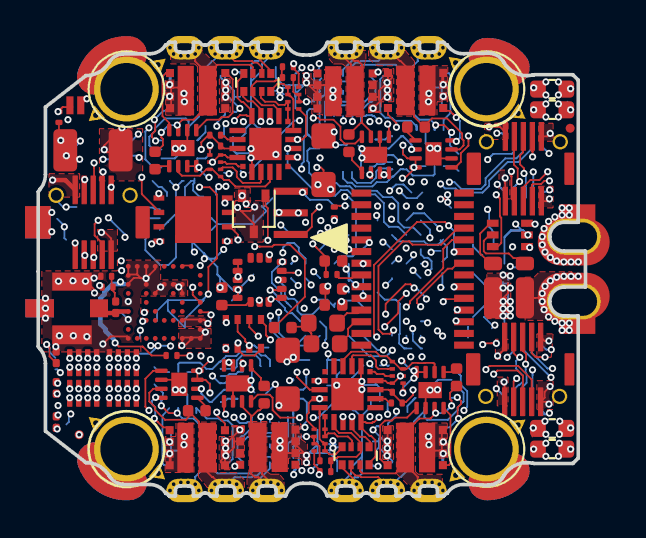
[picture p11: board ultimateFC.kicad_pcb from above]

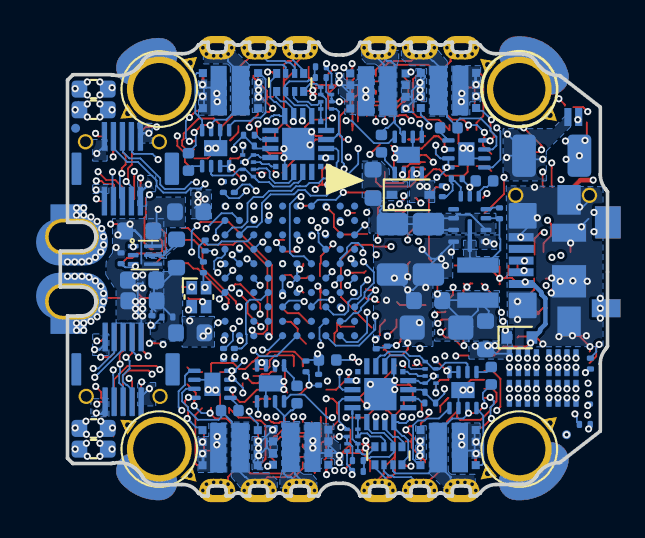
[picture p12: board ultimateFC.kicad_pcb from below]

Board: 8 copper layers, 30.4 x 25.2 mm, 186 parts (94 on the bottom side), 191 nets.

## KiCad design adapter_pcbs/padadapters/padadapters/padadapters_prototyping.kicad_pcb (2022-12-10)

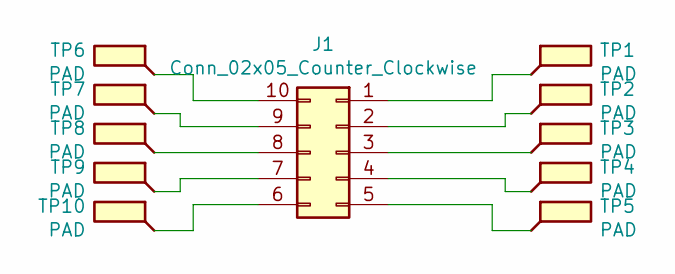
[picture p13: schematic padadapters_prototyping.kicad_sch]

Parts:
J1: Conn_02x05_Counter_Clockwise; 10132797-011100LF_mod_small_adapter_pads
TP1, TP2, TP3, TP4, TP5, TP6, TP7, TP8, TP9, TP10: PAD; TestPoint_Pad_1.2x2.5mm

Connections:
unnamed: J1.1, TP1.1
unnamed: J1.2, TP2.1
unnamed: J1.4, TP4.1
unnamed: J1.5, TP5.1
unnamed: J1.6, TP10.1
unnamed: J1.7, TP9.1
unnamed: J1.8, TP8.1
unnamed: J1.9, TP7.1
unnamed: J1.10, TP6.1
unnamed: J1.3, TP3.1

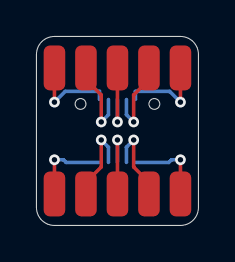
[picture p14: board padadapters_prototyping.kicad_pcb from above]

Board: 2 copper layers, 9.0 x 10.5 mm, 11 parts (1 on the bottom side), 10 nets.

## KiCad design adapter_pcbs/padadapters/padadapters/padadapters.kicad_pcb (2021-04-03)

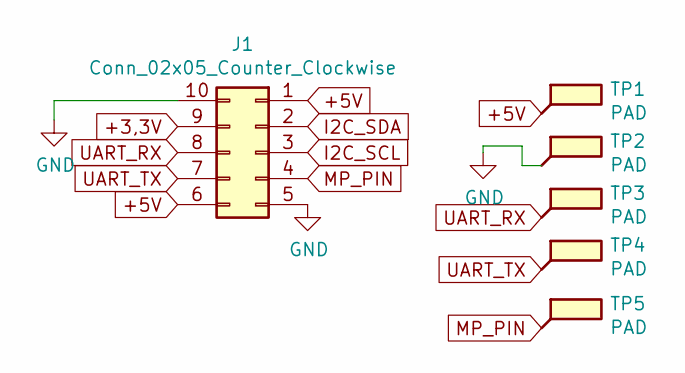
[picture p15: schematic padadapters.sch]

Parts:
J1: Conn_02x05_Counter_Clockwise; 10132797-011100LF_mod_small_adapter_pads
TP1, TP2, TP3, TP4, TP5: PAD; TestPoint_Pad_1.2x2.5mm

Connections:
+3,3V: J1.9
+5V: J1.1, J1.6, TP1.1
GND: J1.5, J1.10, TP2.1
I2C_SCL: J1.3
I2C_SDA: J1.2
MP_PIN: J1.4, TP5.1
UART_RX: J1.8, TP3.1
UART_TX: J1.7, TP4.1

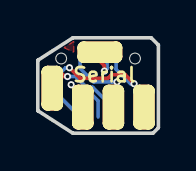
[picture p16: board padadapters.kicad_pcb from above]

Board: 2 copper layers, 6.7 x 5.3 mm, 6 parts (1 on the bottom side), 5 nets.

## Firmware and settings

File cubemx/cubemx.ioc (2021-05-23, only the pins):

Mcu.UserName=STM32F745VGHx
PA0/WKUP.Signal=UART4_TX
PA1.Signal=UART4_RX
PA11.Signal=USB_OTG_FS_DM
PA12.Signal=USB_OTG_FS_DP
PA15.Signal=SPI3_NSS
PA2.Signal=S_TIM2_CH3
PA3.Signal=S_TIM2_CH4
PA5.Signal=ADCx_IN5
PA6.Signal=S_TIM3_CH1
PA7.Signal=S_TIM3_CH2
PA9.Signal=USB_OTG_FS_VBUS
PB0.Signal=S_TIM3_CH3
PB1.Signal=S_TIM3_CH4
PB10.Signal=I2C2_SCL
PB11.Signal=I2C2_SDA
PB12.Signal=SPI2_NSS
PB13.Signal=SPI2_SCK
PB14.Signal=SPI2_MISO
PB15.Signal=SPI2_MOSI
PB3.Signal=GPIO_Output
PB4.Signal=GPIO_Output
PB6.Signal=USART1_TX
PB7.Signal=USART1_RX
PC10.Signal=SPI3_SCK
PC11.Signal=SPI3_MISO
PC12.Signal=SPI3_MOSI
PC5.Signal=ADCx_IN15
PC6.Signal=USART6_TX
PC7.Signal=USART6_RX
PD0.Signal=GPIO_Input
PD12.Signal=S_TIM4_CH1
PD13.Signal=S_TIM4_CH2
PD2.Signal=UART5_RX
PD5.Signal=USART2_TX
PD6.Signal=USART2_RX
PD7.Signal=GPIO_Input
PD8.Signal=USART3_TX
PD9.Signal=USART3_RX
PE0.Signal=UART8_RX
PE1.Signal=UART8_TX
PE11.Signal=S_TIM1_CH2
PE13.Signal=S_TIM1_CH3
PE14.Signal=S_TIM1_CH4
PE2.Signal=SPI4_SCK
PE4.Signal=SPI4_NSS
PE5.Signal=SPI4_MISO
PE6.Signal=SPI4_MOSI
PE7.Signal=UART7_RX
PE8.Signal=UART7_TX
PE9.Signal=S_TIM1_CH1
PH0/OSC_IN.Signal=RCC_OSC_IN
PH1/OSC_OUT.Signal=RCC_OSC_OUT

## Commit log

2020-05-26 move design files to /kicad
    [10132797-011100LF.stp, 10132797-021100LF.stp, MCU.sch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]
2020-09-12 modified: kicad/MCU.sch modified: kicad/OSD.sch modified: kicad/Sensors.sch modified: kicad/sym-lib-table modified: kicad/ultimateFC-cache.lib modified: kicad/ultimateFC.kicad_pcb modified: kicad/ult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
    [MCU.sch, OSD.sch, Sensors.sch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]
2021-03-10 status 2021-03-10
    [ultimateFC.kicad_pcb, ultimateFC.sch]
2021-03-14 changed pin for voltage ADC
    [ultimateFC.kicad_pcb]
2021-03-28 updated to version 2
    [ultimateFC.sch, ultimateFC_v1.kicad_pcb, ultimateFC_v2.kicad_pcb]
2021-04-03 changed motor pins for more TIMER/ DMA / ADC Support
    [10132797-011110LF.stp, 10132798-011110LF.stp, layer_buildup.xls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]
2021-04-03 added price estimation
    [price_estimatioen_mouser.xls]
2021-04-04 Cleaned up a bit
    [10132797-011100LF.stp, 10132797-021100LF.stp, MCU.sch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]
2021-04-12 added images
    [price_estimation_mouser.xls, ultimateFC.kicad_pcb]
2021-04-22 changed 3.3V dcdc converter to one with forced pwm
    [ultimateFC.kicad_pcb, ultimateFC.sch]
2021-04-22 swap ESC gate role names, add schematic pdf
    [ultimateFC.kicad_pcb, ultimateFC.sch]
2021-04-24 add license info to schematic, add schematic pdf
    [ultimateFC.sch]
2021-04-25 exported gerbers and p+p files, started whoop mount adapter
    [ultimateFC-B_Cu.gbr, ultimateFC-B_Mask.gbr, ultimateFC-B_Paste.gbr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]
2021-05-13 added diode on 5V DCDC input
    [ultimateFC.kicad_pcb, ultimateFC.sch, whoop_mounting_adapter.kicad_pcb]
2021-05-13 added comment about diode alternative
    [ultimateFC.sch]
2021-05-13 changed some minor pcb things
    [ultimateFC.kicad_pcb]
2021-05-13 added a few 3d components
    [idc.stp, ultimateFC.kicad_pcb]
2021-08-04 add drill/placement origin add assembly_output/*.pos
    [ultimateFC.kicad_pcb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]
2021-08-23 fix footprints (surface mount flag) fix IDC centers update assembly_out/*.pos
    [ultimateFC.kicad_pcb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]
2021-08-24 fix IDC routing, add fiducials to pos file
    [ultimateFC.kicad_pcb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]
2021-08-24 fix fidu centers, update pos files
    [ultimateFC.kicad_pcb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]
2022-03-27 update pcb to KiCad6 add assembly_output/gerbers
    [ultimateFC.kicad_pcb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]
2022-12-10 add prototyping bergstak adapter
    [padadapters_prototyping.kicad_pcb, padadapters_prototyping.kicad_sch]
2023-05-01 some minor updates
    [ultimateFC.sch]
2023-05-01 add C0201 and R0201 paste
    [ultimateFC.kicad_pcb, ultimateFC.kicad_sch]

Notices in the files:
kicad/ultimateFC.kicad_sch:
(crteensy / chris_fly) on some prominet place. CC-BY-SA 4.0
